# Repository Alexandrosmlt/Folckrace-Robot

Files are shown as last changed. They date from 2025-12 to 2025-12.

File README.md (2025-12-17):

# Folckrace Robot

## 1. Project Overview

#### This is an autonomous robot made for Folkrace (which is a robot competition centered around autonomous racing and steering skills). My design features 4 HS DC Motors paired with 5 ToF sensors, providing precise feedback in real time.

## 1.1 Why i am building this project

#### I am making this project to get real-life experience in developing complex systems and working with fast robotics controls. This project is great to help me improve my skills in putting together microcontrollers, motor drivers and sensors in order to create a autonomous and competitive robot.

## 2. Hardware and Design

### 2.1 3D Visualization

* **Front View**:

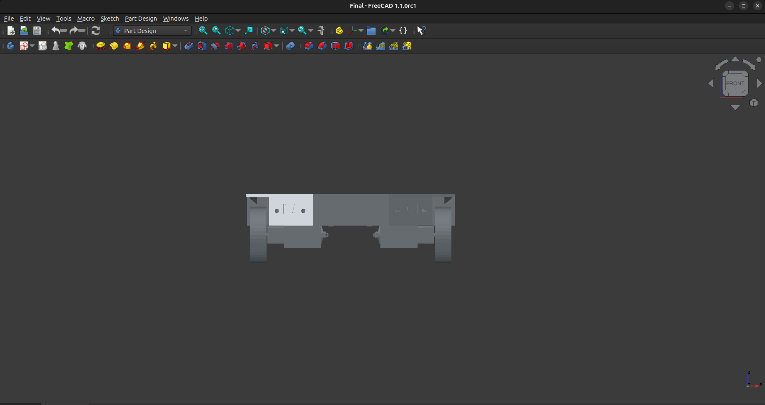
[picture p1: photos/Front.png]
Front

* **Rear View**:

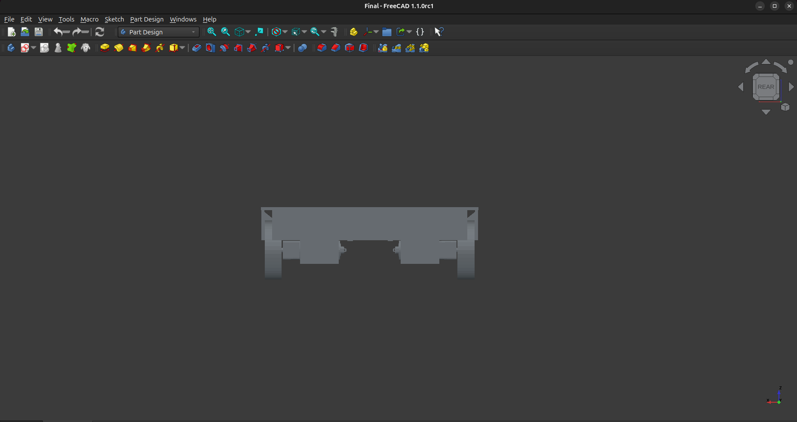
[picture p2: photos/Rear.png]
Rear

* **Right View**:

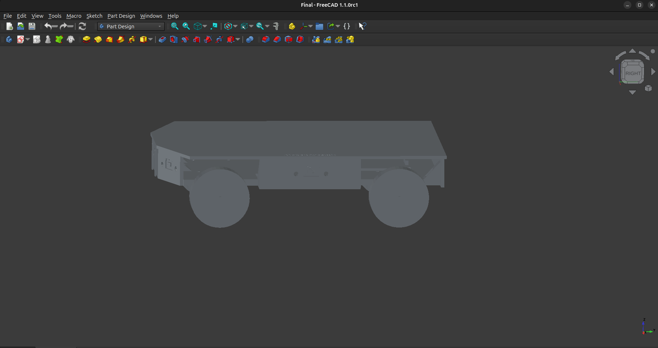
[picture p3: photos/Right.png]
Right

* **Left View**:

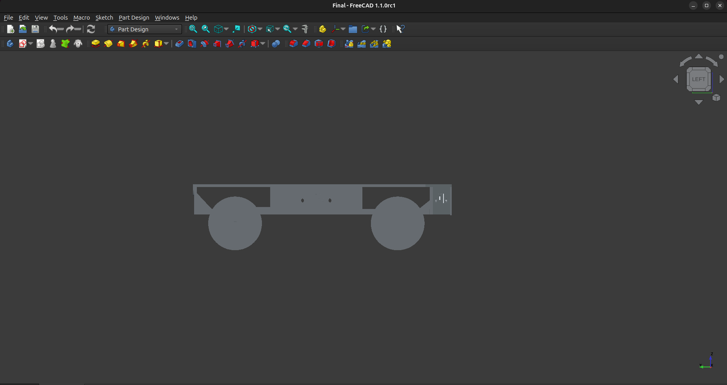
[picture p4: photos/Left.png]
Left

* **Final View**:

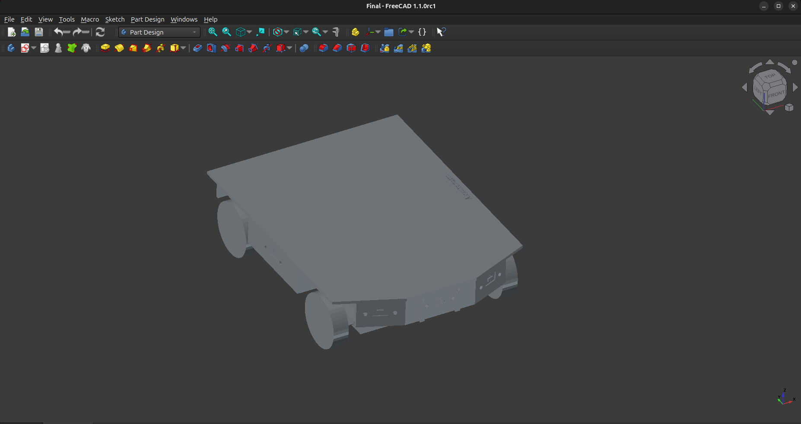
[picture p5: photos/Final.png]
Final


### 2.2 Custom PCB 

* **PCB Top View**:

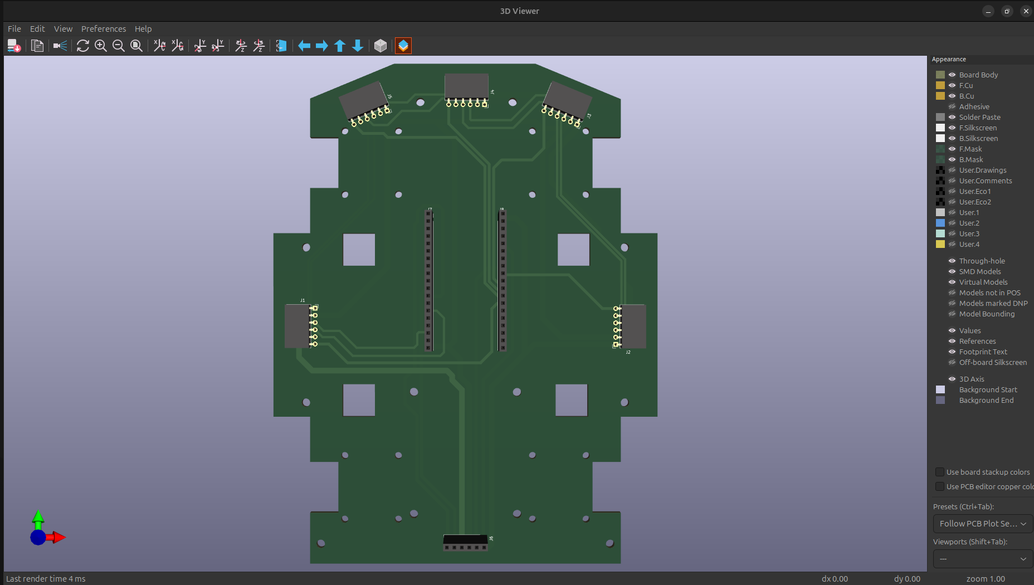
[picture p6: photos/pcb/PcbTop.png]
Top


* **PCB Bottom View**:

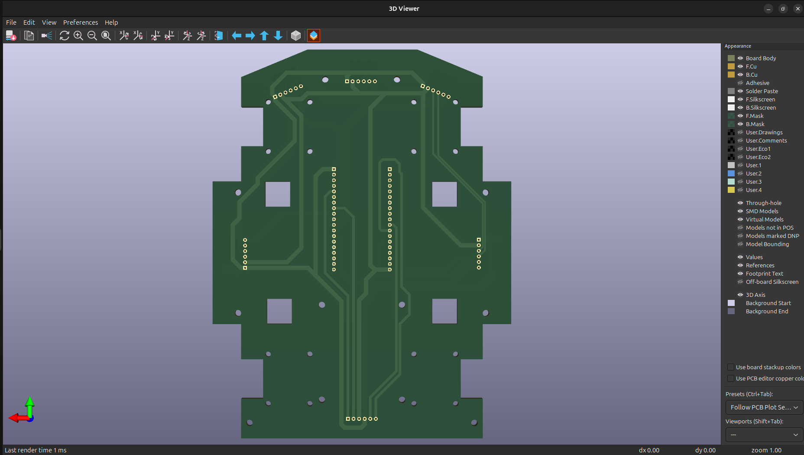
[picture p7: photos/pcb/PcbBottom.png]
Bottom


* **PCB Schematic**:

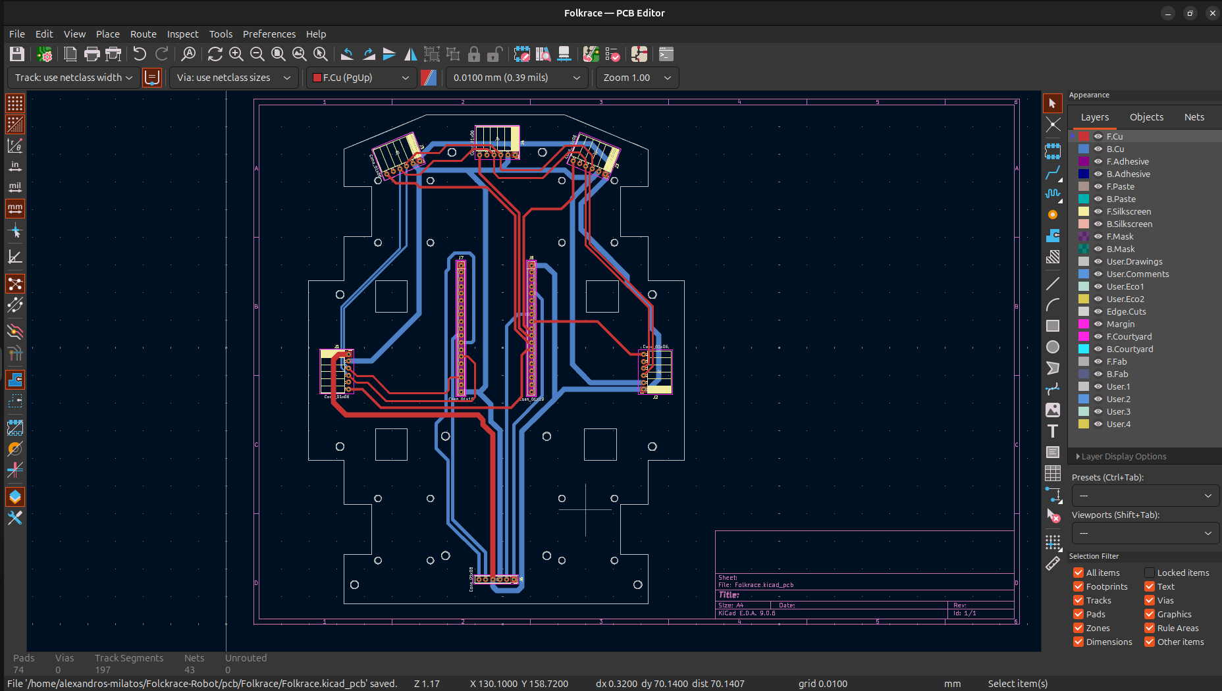
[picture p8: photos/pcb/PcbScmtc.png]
Schematic


### 2.3 Wiring Diagram

* **Wiring diagram**:

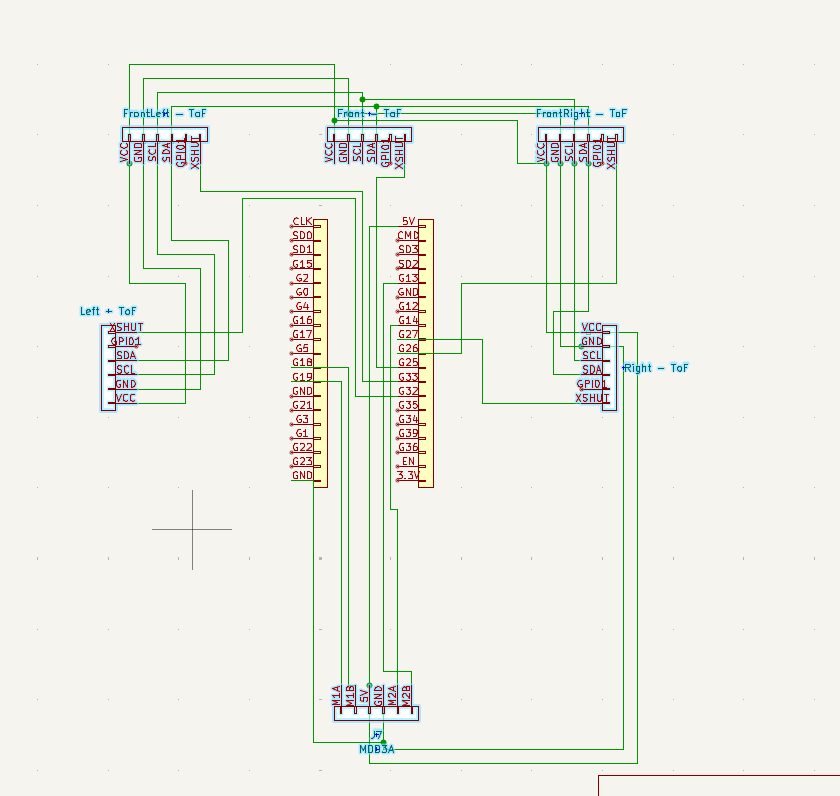
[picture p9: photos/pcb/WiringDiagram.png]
Wires!!


### 2.4 Pinout

#### 1. ToF Sensor Connections (5 Sensors)

>| Component | Function | ESP32 Pin |
>| :--- | :--- | :--- |
>| **I2C Bus** | Data Line (SDA) | **GPIO 21** |
>| **I2C Bus** | Clock Line (SCL) | **GPIO 22** |
>| ToF 1 | XSHUT Pin | **GPIO 33** |
>| ToF 2 | XSHUT Pin | **GPIO 32** |
>| ToF 3 | XSHUT Pin | **GPIO 27** |
>| ToF 4 | XSHUT Pin | **GPIO 26** |
>| ToF 5 | XSHUT Pin | **GPIO 25** |

#### Motor Driver (MDD3A)

>| MDD3A | Motor | Function | ESP32 Pin |
>| :--- | :--- | :--- | :--- |
>| M1A | Motor 1 | Forward Speed | **GPIO 19** |
>| M1B | Motor 1 | Reverse Speed | **GPIO 18** |
>| M2A | Motor 2 | Forward Speed | **GPIO 14** |
>| M2B | Motor 2 | Reverse Speed | **GPIO 13** |

#### 3. Total Used Pins

>| Type | Pin Numbers Used | Total |
>| :--- | :--- | :--- |
>| **Motor Driver (PWM)** | 19, 18, 14, 13 | 4 |
>| **I2C** | 21, 22 | 2 |
>| **ToF XSHUT** | 33, 32, 27, 26, 25 | 5 |
>| **TOTAL GPIO PINS USED** | | **11** |

## 3.Filmware

### Summury of [Code](/firmware/Folkrace.ino) (**NOT TESTED**):

#### 1.Setup: The ESP32 initializes Wi-Fi, OTA and I2C bus and configures all ToF's and assigns them a unique addresses.

#### 2.Imput: The main loop is reading the distance from all the sensors and compines them using weighted coefficients to calculate a single positional error.

#### 3.Control: It gets the error and feeds it in the PID controller, which calculates the correction needed to reduce the error to 0.

#### 4.Output: The correction finaly is applied to the motors using PWM signals.

## 3.1 Parts that require [3D printing](/STLs)

### Parts List:

* **[Front Bumper](/STLs/FrontBumper.stl)** (Quantity: 1)
* **[Rear Bumper](/STLs/RearBumper.stl)** (Quantity: 1)
* **[Side Bumpers](/STLs/SideBumper.stl)** (Quantity: 2)
* **[Motor Mounts](/STLs/MotorMount.stl)** (Quantity: 4)

<!-- ## 4. Bill of Materials (BOM)

| Item | Description | Quantity | Unit Price (€) | Total Price (€) | URL | Running Total (€ with Tax) |
| :--- | :--- | :--- | :--- | :--- | :--- | :--- |
| **DC Motors** | Drive Motors (6V 750RPM) | 4 | 16.00 | 64.00 | [https://www.jsumo.com](https://www.jsumo.com/core-dc-motor-6v-750rpm) | 64.00 |
| **Wheels** | Aluminum - Silicone Wheel Set | 2 | 15.50 | 31.00 | [https://www.jsumo.com](https://www.jsumo.com/jsumo-wheel-43x11mm-pair-soft-silicone) | 95.00 |
| **Microcontroller** | ESP32-DevKitC Development Board | 1 | 9.90 | 9.90 | [https://grobotronics.com](https://grobotronics.com/esp32-development-board-devkit-v1.html) | 104.90 |
| **Sensors** | VL53L0X Time-of-Flight (ToF) | 5 | 2.50 | 12.50 | [https://www.temu.com](https://www.temu.com/ul/kuiper/un9.html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) | 117.40 |
| **Motor Driver** | Cytron MDD3A | 1 | 8.50 | 8.50 | [https://botland.store](https://botland.store/motor-drivers-modules/15819-cytron-mdd3a-dual-channel-16v-3a-motor-controller-5904422324841.html) | 125.90 |
| **Battery** | Battery Lithium 18650 | 2 | 5.80 | 11.60 | [https://grobotronics.com](https://grobotronics.com/battery-lithium-18650-3.6v-3200mah-lg-inr18650-mh1.html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) | 137.50 |
| **Battery Holder** | Battery Holder 2×18650 with Plug 5.5×2.1 | 1 | 1 | 1 | [https://grobotronics.com](https://grobotronics.com/battery-holder-218650-with-plug-5-5x2-1.html) | 138.50 |
| **Pin Header** | Pin Header Female 1x6 2.54mm | 6 | 0.08 | 0.64 | [https://grobotronics.com](https://grobotronics.com/pin-header-1x6-female-2.54mm.html) | 139.14 |
| **Pin Header** | Pin Header 1x20 Female 2.54mm| 2 | 0.25 | 0.50 | [https://grobotronics.com](https://grobotronics.com/pin-header-1x20-female-2.54mm.html) | 139.64 |
| **PCB Manufacturing** | PCBWay | 5 | $47.78 | $75.75 | [https://www.pcbway.com](https://www.pcbway.com/QuickOrderOnline.aspx) | 215.39 |
 -->

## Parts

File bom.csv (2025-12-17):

Item | Description | Quantity | Notes
DC Motors | Drive motors (6V 750RPM) | 4 | Main drive motors
Wheels | Aluminum wheels with soft silicone | 2 | Compatible with DC motors
ESP32 Dev Board | ESP32-DevKitC development board | 1 | Main microcontroller, handles control logic
VL53L0X ToF Sensors | Time-of-Flight distance sensors | 5 | Used for obstacle detection / sensing
Cytron MDD3A Motor Driver | Dual channel 3A motor driver | 1 | Controls DC motors with PWM
18650 Lithium Batteries | 3.6V 18650 Li-ion cells | 2 | Main power source
Battery Holder | 2x18650 battery holder with DC plug | 1 | Holds and powers the system
Female Pin Headers 1x6 | 2.54mm female headers | 6 | For sensor and board connections
Female Pin Headers 1x20 | 2.54mm female headers | 2 | For ESP32 and PCB connections
Custom PCB | Manufactured PCB (PCBWay) | 5 | Main circuit boards

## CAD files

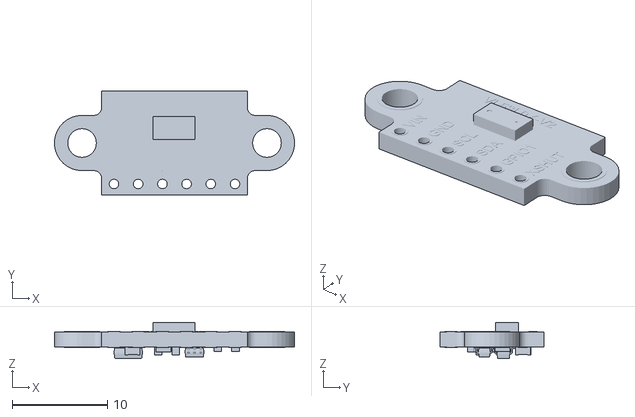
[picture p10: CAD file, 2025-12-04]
cad/3D parts/VL53L0X-V2.stl
25.2 x 10.9 x 3.80

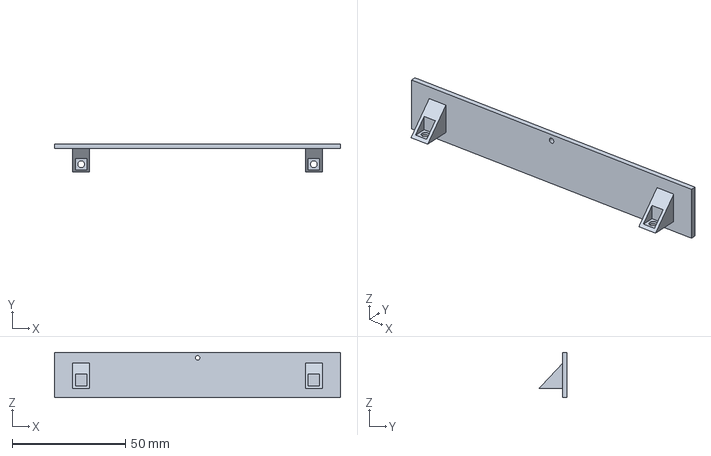
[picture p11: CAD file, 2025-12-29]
cad/RearBumper.FCStd
126.0 x 12.5 x 20.0 mm

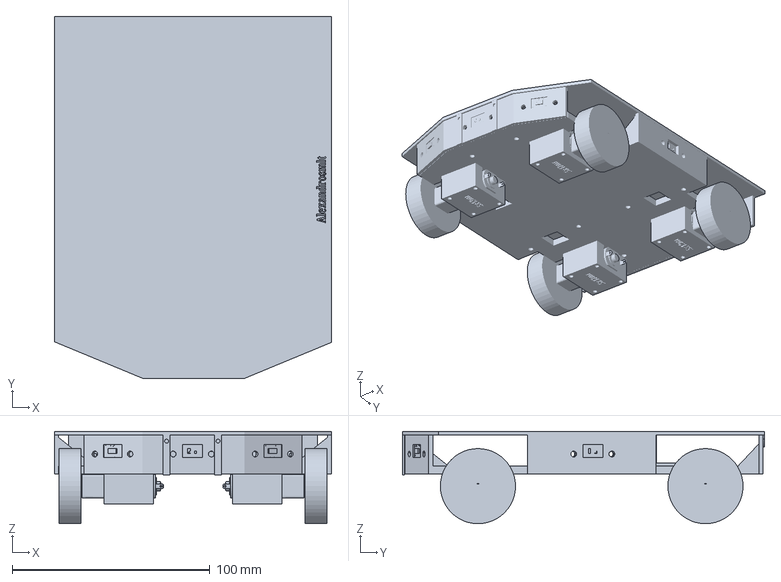
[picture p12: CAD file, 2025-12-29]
cad/Final.FCStd
140.1 x 183.1 x 46.7 mm

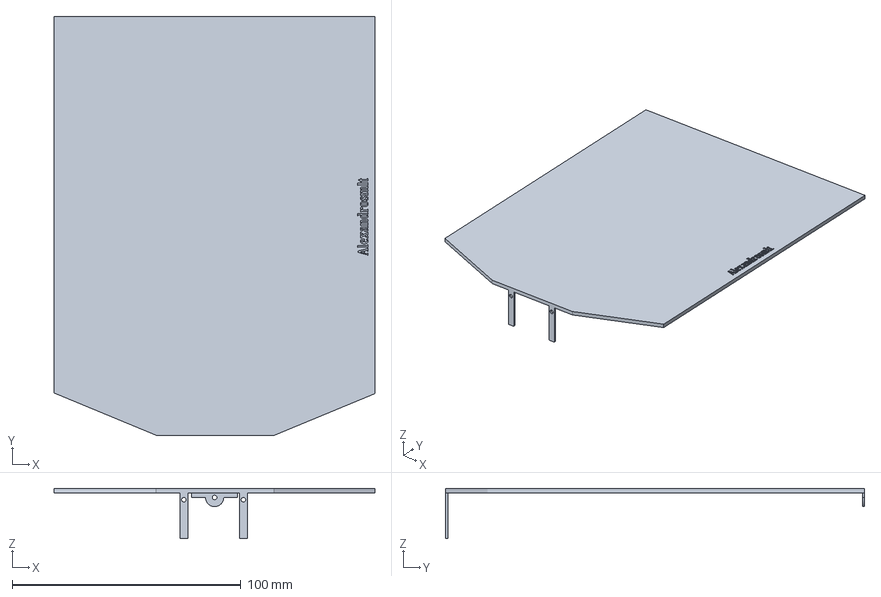
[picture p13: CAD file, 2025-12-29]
cad/TopCover.FCStd
140.1 x 183.0 x 22.0 mm

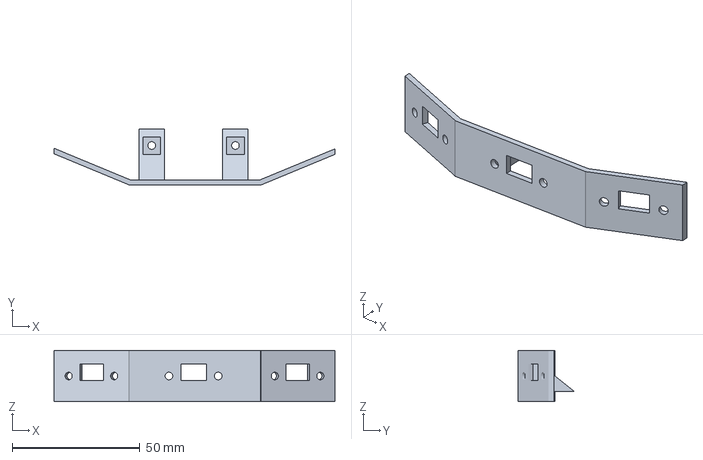
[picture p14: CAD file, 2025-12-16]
cad/FrontBumper.FCStd
110.0 x 22.0 x 20.0 mm

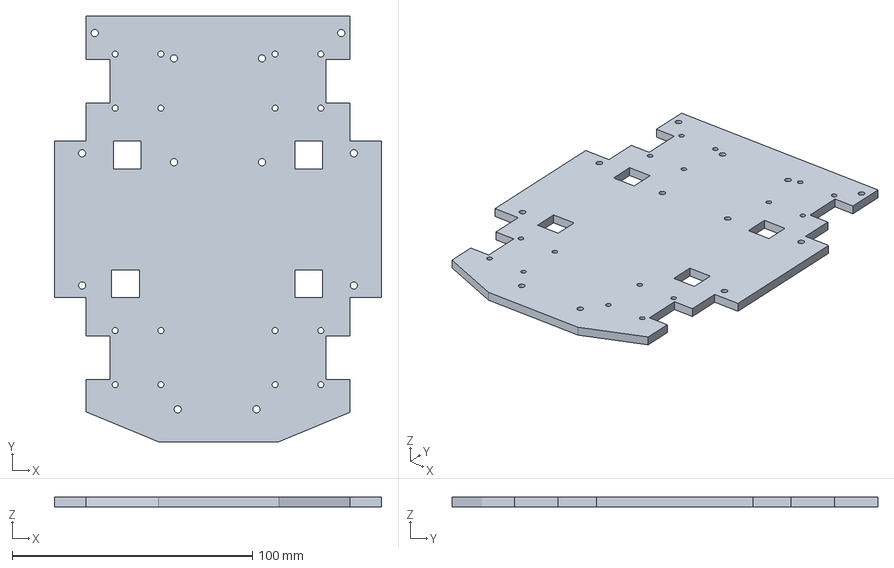
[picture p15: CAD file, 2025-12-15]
cad/Base.FCStd
136.0 x 177.0 x 4.00 mm

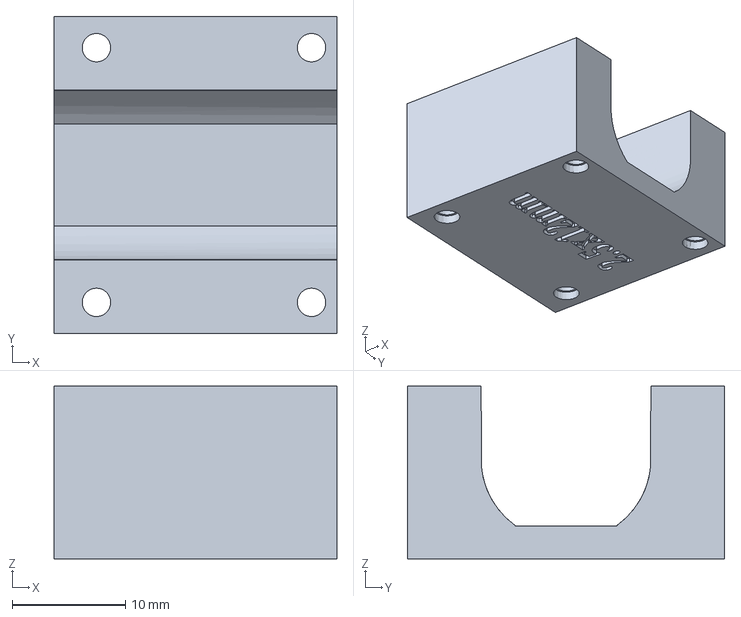
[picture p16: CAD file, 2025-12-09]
cad/MotorMount.FCStd
25.0 x 28.0 x 15.2 mm

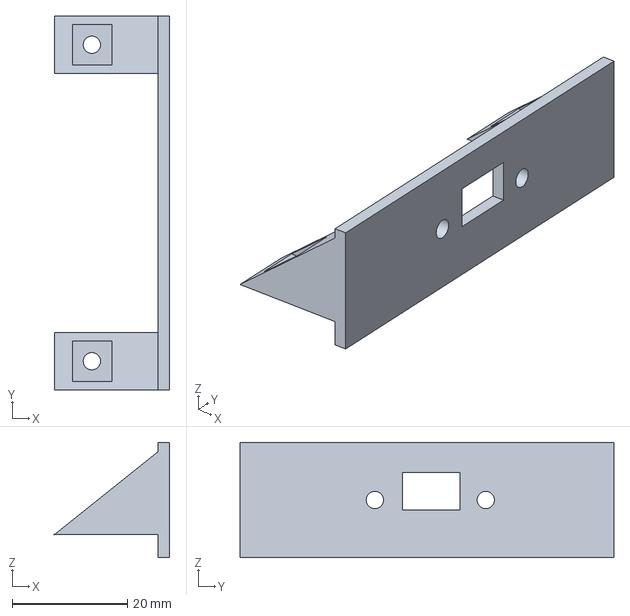
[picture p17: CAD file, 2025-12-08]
cad/SideBumper.FCStd
20.0 x 65.0 x 20.0 mm

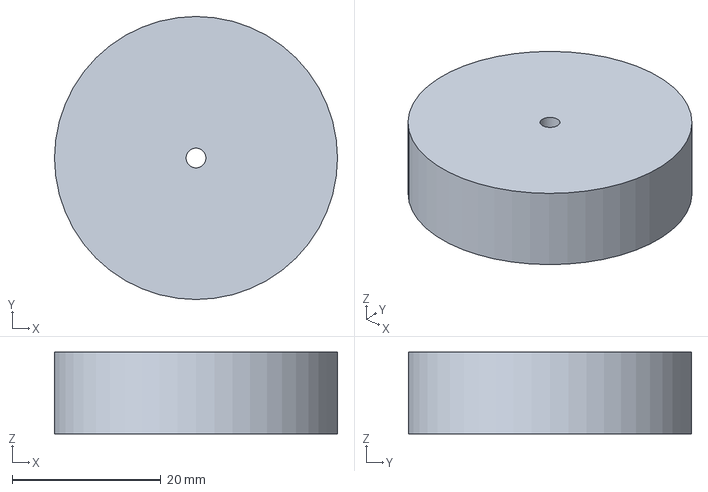
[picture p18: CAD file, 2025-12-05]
cad/Wheel.FCStd
38.0 x 38.0 x 11.0 mm

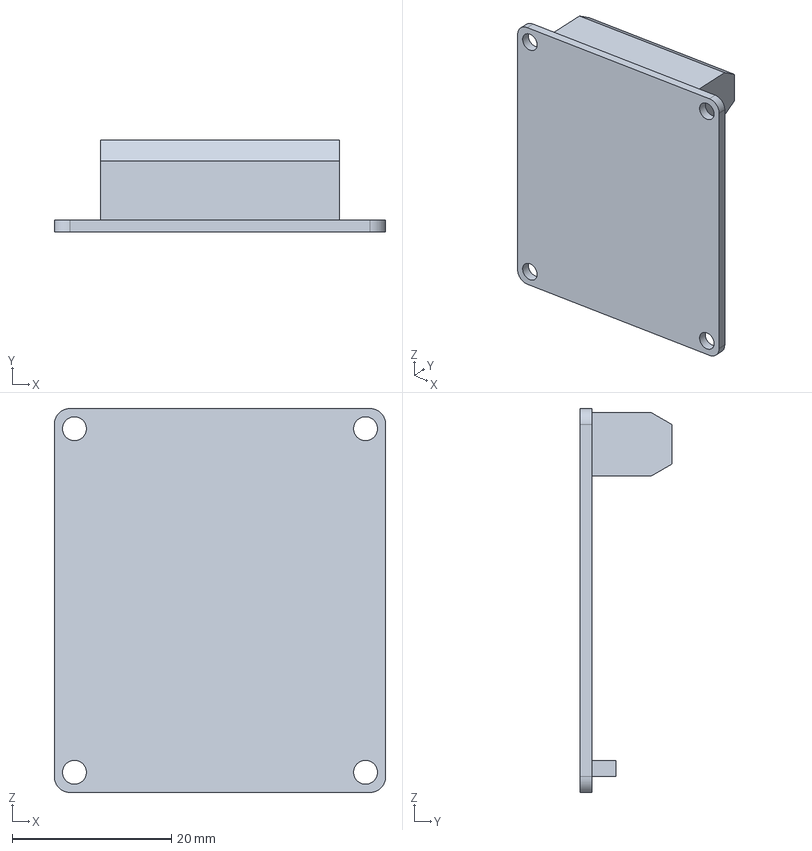
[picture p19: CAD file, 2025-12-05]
cad/CYTRON-MDD3A.FCStd
41.7 x 11.5 x 48.3 mm

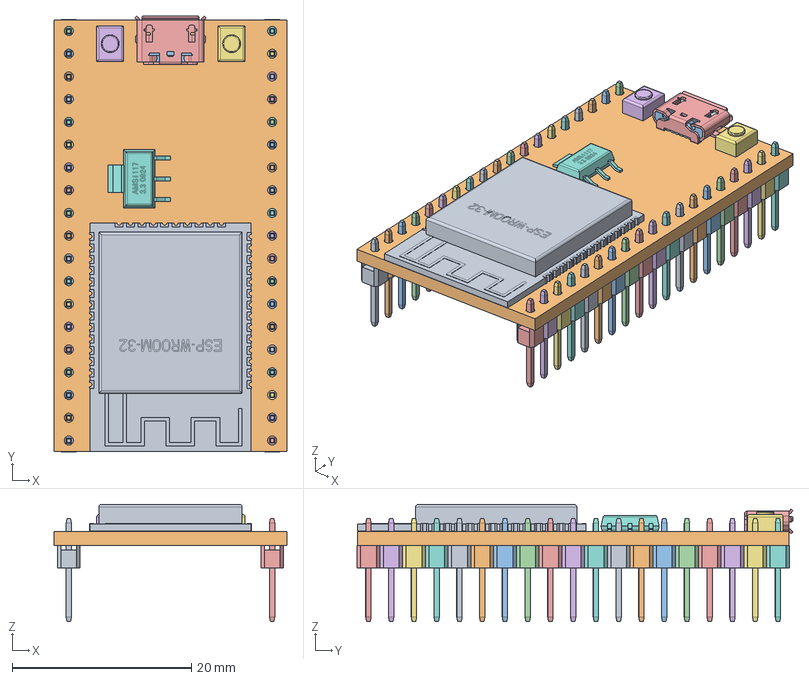
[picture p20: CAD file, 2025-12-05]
cad/ESP32.FCStd
26.0 x 48.7 x 13.1 mm
KiCAD-ESP-WROOM-32
ESP32 PCB
molex_0473460001
molex_0473460002
molex_0473460003
button
button001
AMS1117
HEADER10P
HEADER10P001
HEADER10P002
HEADER10P003
HEADER10P004
HEADER10P005
HEADER10P006
HEADER10P007
HEADER10P008
HEADER10P009
HEADER10P011
HEADER10P012
HEADER10P013
HEADER10P014
HEADER10P015
HEADER10P016
HEADER10P017
HEADER10P018
HEADER10P019
HEADER10P020
HEADER10P022
HEADER10P023
HEADER10P024
HEADER10P025
HEADER10P026
HEADER10P027
HEADER10P028
HEADER10P029
HEADER10P030
HEADER10P031
HEADER10P033
HEADER10P034
HEADER10P035
HEADER10P036
HEADER10P037
HEADER10P038
HEADER10P039
HEADER10P040
HEADER10P041
HEADER10P042

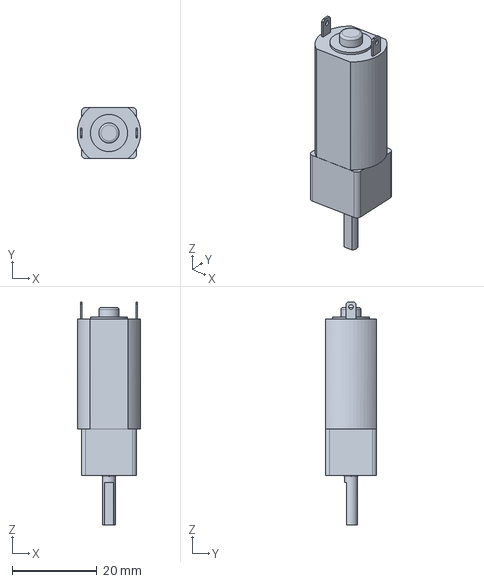
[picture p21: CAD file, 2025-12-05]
cad/DcMotor.FCStd
15.0 x 12.1 x 52.7 mm

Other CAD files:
cad/BaseTraces.FCStd
cad/VL53L0X.FCStd
STLs/FrontBumper.stl
STLs/MotorMount.stl
STLs/RearBumper.stl
STLs/SideBumper.stl
cad/3D parts/Base.stl
cad/3D parts/CYTRON-MDD3A.stl
cad/3D parts/DcMotor.stl
cad/3D parts/ESP32.stl
cad/3D parts/Final.stl
cad/3D parts/MotorMount.stl
cad/3D parts/RearBumper.stl
cad/3D parts/TopCover.stl
cad/3D parts/Wheel.stl

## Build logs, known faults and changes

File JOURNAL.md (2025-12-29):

## FOLCKRACE ROBOT

## Total Time Spent: ~ 15h

# UPDATES

**Date:** 2025-12-29

### Task: Hardware Modeling
* **Component:** Rear Bumper Bumpers
* **Work Performed:** Made a 2mm hole for the screw from `TopCover.stl`
* **File Output:** `RearBumper.stl`
* **Status:** Complete
* **Time Spent:** ~0.40h
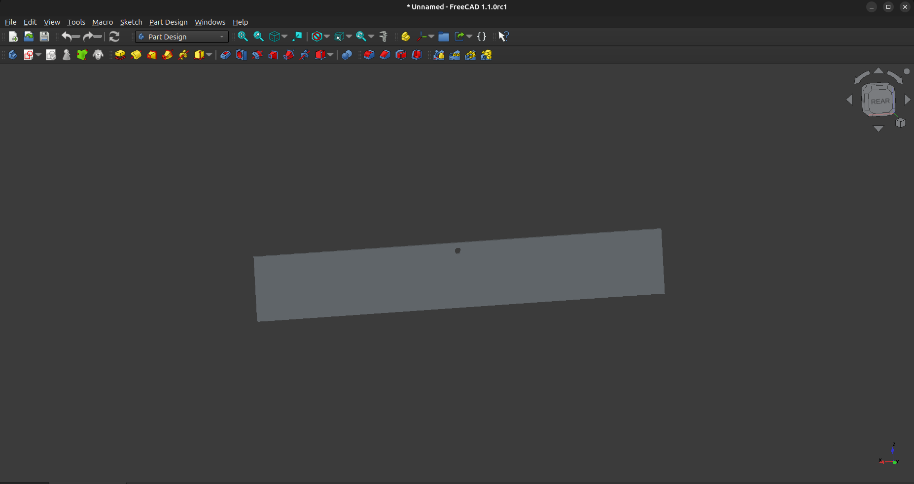
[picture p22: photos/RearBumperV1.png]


### Task: Hardware Modeling
* **Component:** Top Cover
* **Goal:** Make something to cover the top of the robot 
* **Work Performed:** Made the top cover for the robot
* **File Output:** `TopCover.stl`
* **Status:** Complete.
* **Time Spent:** ~0.40h
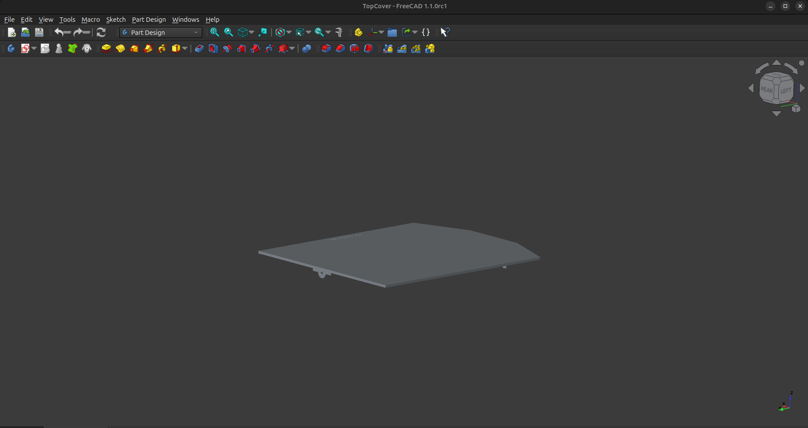
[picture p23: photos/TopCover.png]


**Date:** 2025-12-16

### Task: Filmware
* **Goal:** Make The code for the ESP32
* **Work Performed:** Made a completed version for the Robot that uses OTA for updates and PID to calculate the weight which gets processed and drives the motors to zero error.
* **Status:** Complete.
* **Time Spent:** ~1.30h
* [Code](/firmware/Folkrace.ino)

# PCB MODELING COMPLETED

## **Final PCB:**

Final

# CUSTOM PCB

### Task: PCB Modeling
* **Component:** PCB
* **Goal:** Finish the PCB.
* **Work Performed:** Placed the connectors and connected everything in a 2 layer PCB
* **Status:** Complete.
* **Time Spent:** ~2.30h
Status

**Date:** 2025-12-15

### Task: PCB Modeling
* **Component:** PCB
* **Goal:** Make the edge cuts for the PCB.
* **Work Performed:** Made the edge cuts and added the compoments to the pcb editor
* **Status:** Complete.
* **Time Spent:** ~0.30h
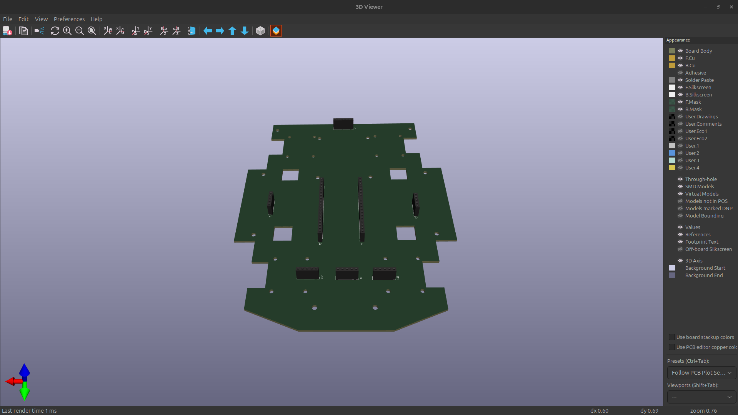
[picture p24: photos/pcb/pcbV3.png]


### Task: Hardware Modeling
* **Component:** Base
* **Goal:** Make .svg for the PCB
* **Work Performed:** Made the base with graphics to put everything together
* **Status:** Complete.
* **Time Spent:** ~0.40h
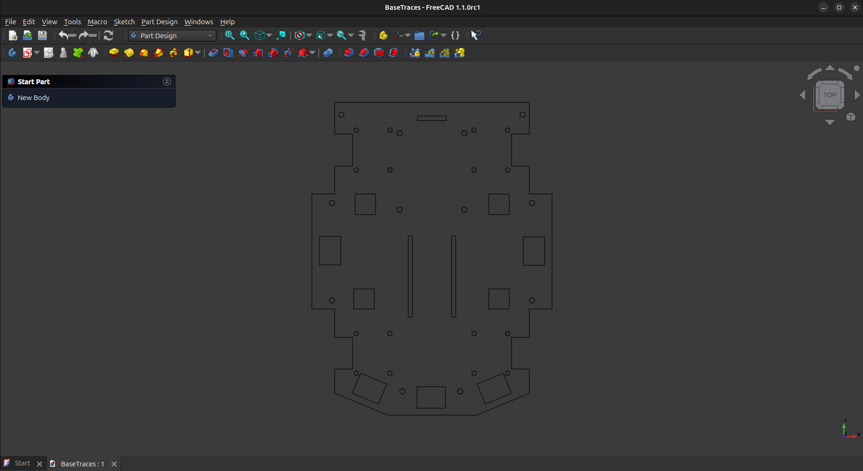
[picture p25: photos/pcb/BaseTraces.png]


**Date:** 2025-12-13

### Task: PCB Modeling
* **Component:** PCB
* **Goal:** Continue making the symbols to start the PCB.
* **Work Performed:** Custom symbols for the ESP32 and MDD3A were created in **KiCAD** and the compoments were all connected together.
* **Status:** Complete.
* **Time Spent:** ~0.50h
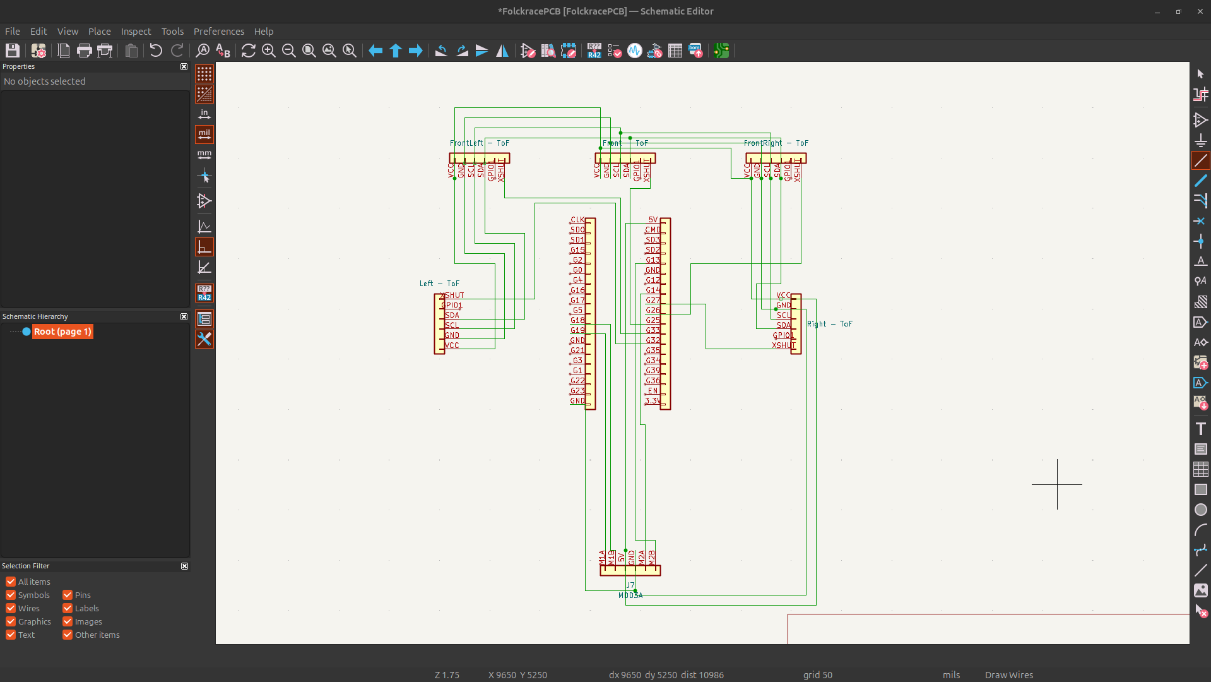
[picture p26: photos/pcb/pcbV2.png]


**Date:** 2025-12-11

### Task: PCB Modeling
* **Component:** PCB
* **Goal:** Make the symbols to start the PCB.
* **Work Performed:** Made a custom symbol for the ToF sensors in **KiCAD**. Next i will create the symbols for the esp32 and mdd3a motor driver
* **Status:** Complete.
* **Time Spent:** ~0.10h
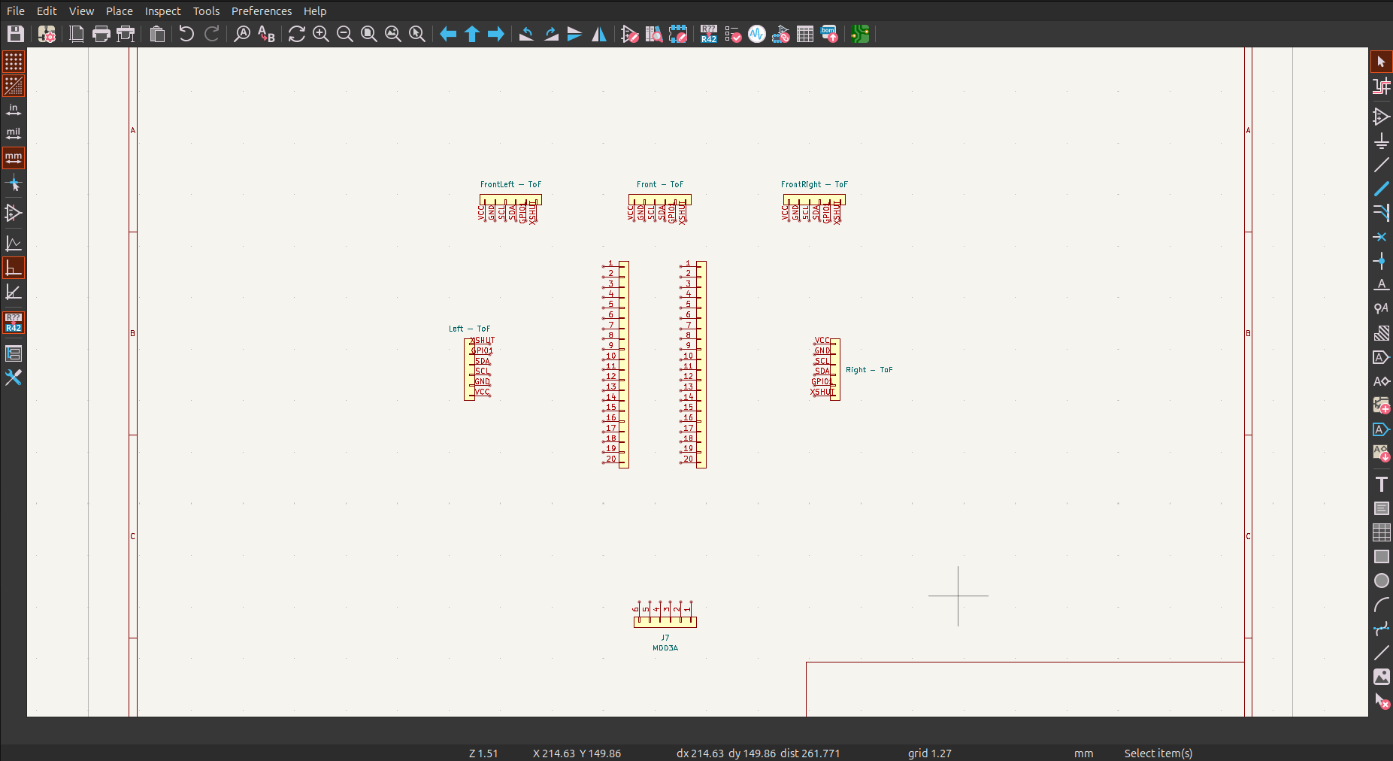
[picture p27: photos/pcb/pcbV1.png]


**Date:** 2025-12-09

# HARDWARE MODELING COMPLETED

## **Final 3D Visualization:**

Final

### Task: Hardware Modeling
* **Component:** Base
* **Goal:** Create a 3D model for the robots base.
* **Work Performed:** Updated the base in **FreeCAD** to include 3mm holes for the `RearBumper.stl`
* **File Output:** `Base.stl`
* **Status:** Complete, Ready for use.
* **Time Spent:** ~0.10h
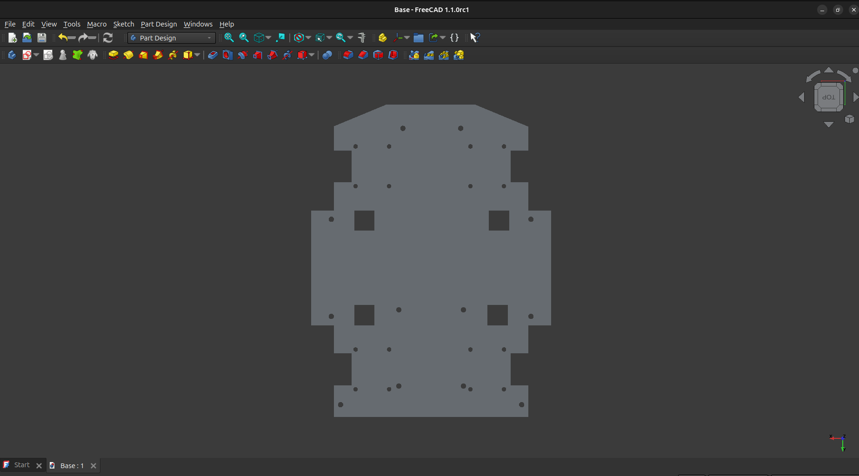
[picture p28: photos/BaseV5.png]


### Task: Hardware Modeling
* **Component:** Side Bumpers
* **Goal:** Create a 3D model for the 2 side sensors to mount on.
* **Work Performed:** Designed a back bumper model in **FreeCAD** to protect the robot 
* **File Output:** `RearBumper.stl`
* **Status:** Complete, Ready for testing 
* **Time Spent:** ~0.40h
Status

### Task: Hardware Modeling
* **Component:** Base
* **Goal:** Create a 3D model for the robots base.
* **Work Performed:** Updated the base in **FreeCAD** to include 11.5mm holes for the motor cables
* **File Output:** `Base.stl`
* **Status:** Complete, Ready for use.
* **Time Spent:** ~0.10h
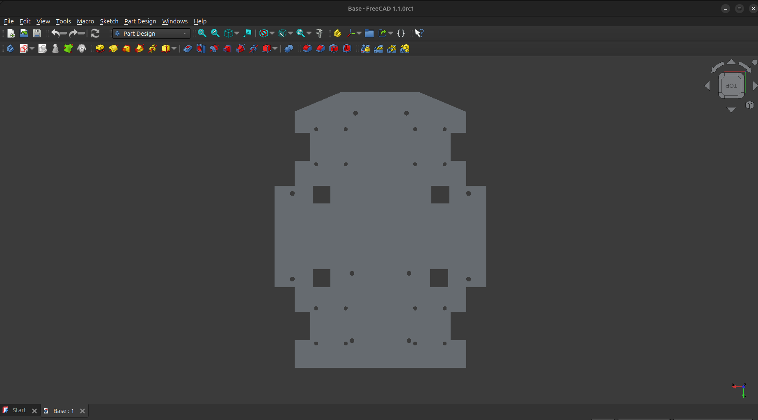
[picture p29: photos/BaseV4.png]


**Date:** 2025-12-08

### Task: Hardware Modeling
* **Component:** Base
* **Goal:** Create a 3D model for the robots base.
* **Work Performed:** Updated the base in **FreeCAD** to include 3mm holes for the motor driver (`CYTRON-MDD3A.stl`)
* **File Output:** `Base.stl`
* **Status:** Complete, Ready for use.
* **Time Spent:** ~0.10h
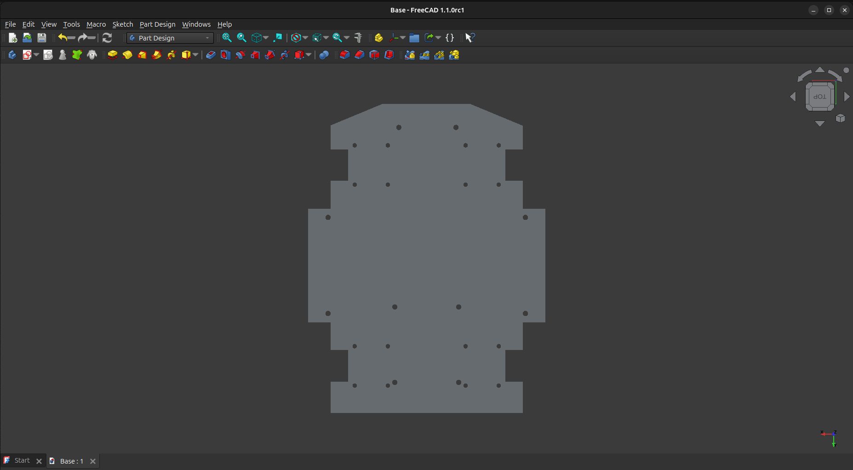
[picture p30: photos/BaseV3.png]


### Task: Hardware Modeling
* **Component:** Base
* **Goal:** Create a 3D model for the robots base.
* **Work Performed:** Updated the base in **FreeCAD** to include 3mm holes for `SideBumper.stl` and `FrontBumper.stl`
* **File Output:** `Base.stl`
* **Status:** Complete, Ready for use.
* **Time Spent:** ~0.30h
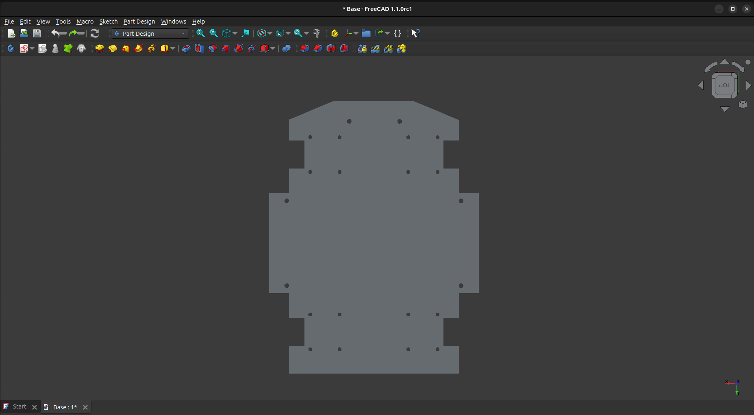
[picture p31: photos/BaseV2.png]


### Task: Hardware Modeling
* **Component:** Side Bumpers
* **Goal:** Create a 3D model for the 2 side sensors to mount on.
* **Work Performed:** Designed a single side bumper model in **FreeCAD** for the ToF sensors to mount on, which is the same for each side of the robot
* **File Output:** `SideBumper.stl`
* **Status:** Complete, Ready for printing 
* **Time Spent:** ~1.00h
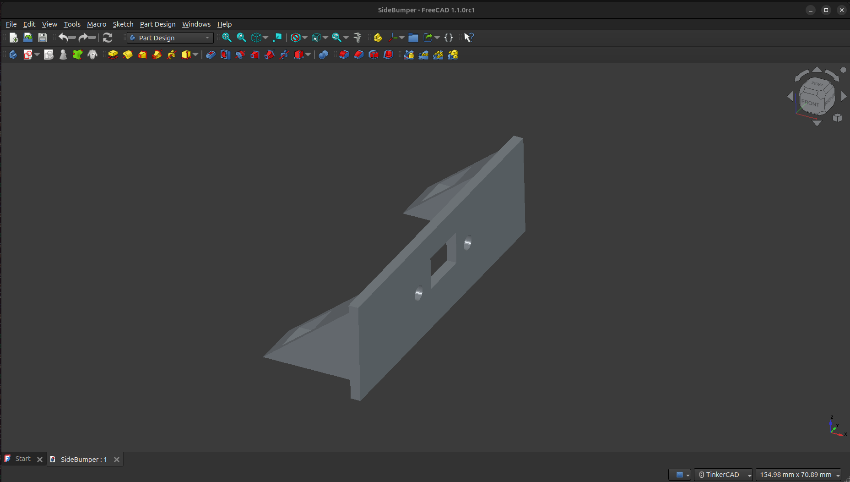
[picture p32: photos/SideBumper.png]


**Date:** 2025-12-06

### Task: Hardware Modeling
* **Component:** Front Bumper
* **Goal:** Create a 3D model for the front sensors to mount on.
* **Work Performed:** Designed a front bumper in **FreeCAD** for the ToF sensors to mount on
* **File Output:** `FrontBumper.stl`
* **Status:** Complete, Ready for printing 
* **Time Spent:** ~1.20h
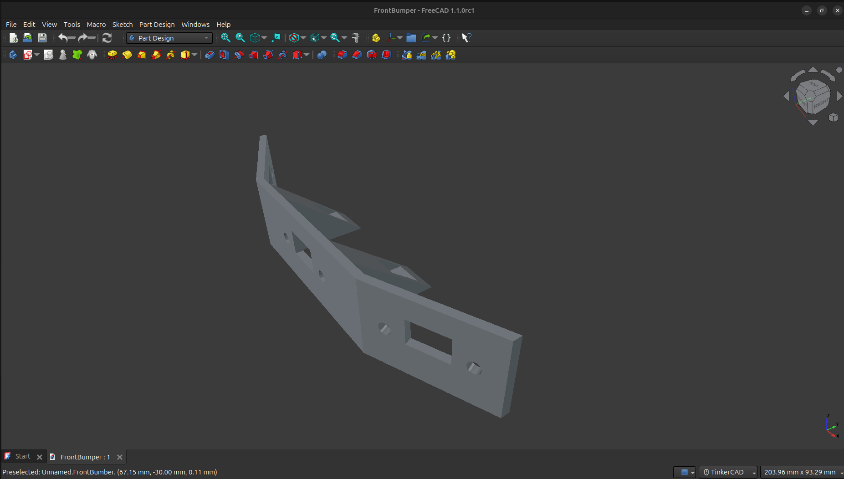
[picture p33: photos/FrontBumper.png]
* **File Output:** `Wheel.stl`

### Task: Hardware Modeling
* **Component:** Base
* **Goal:** Create a 3D model for the robots base.
* **Work Performed:** Designed a base in **FreeCAD** , made holes for `MotorMount.stl` and added space for the wheels
* **File Output:** `Base.stl`
* **Status:** Complete, Ready for use.
* **Time Spent:** ~0.30h
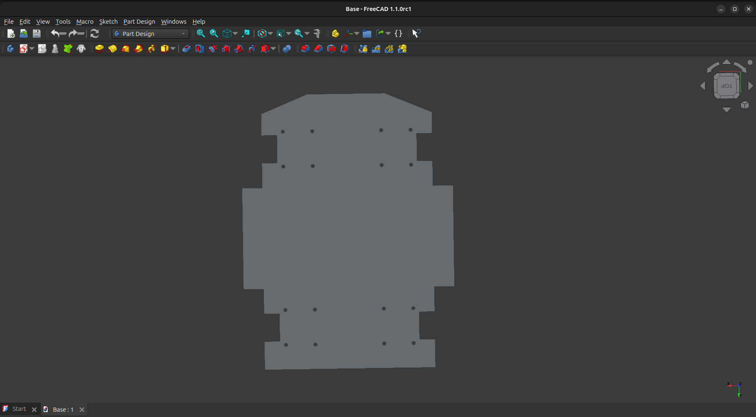
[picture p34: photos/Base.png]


**Date:** 2025-12-05

### Task: Hardware Modeling
* **Component:** Wheels
* **Goal:** Create a 3D model for the wheels
* **Work Performed:** The wheel was modeled in **FreeCAD** 
* **File Output:** `Wheel.stl`
* **Status:** Complete, Ready for import.
* **Time Spent:** ~0.15h
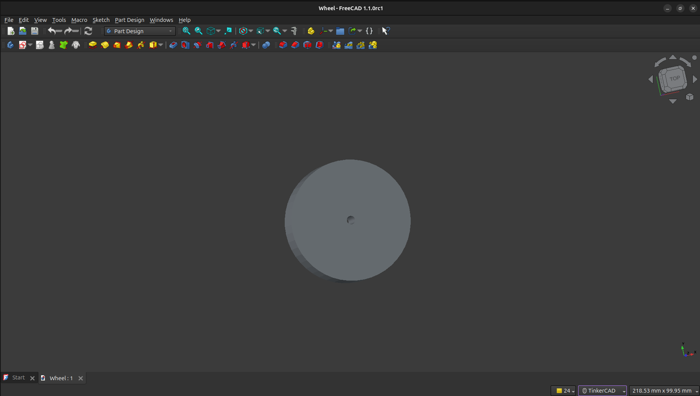
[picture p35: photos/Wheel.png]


### Task: Hardware Modeling
* **Component:** Motor Mount
* **Goal:** Design and create a 3D model for mounting x4 DC Motors to the chassis later on.
* **Work Performed:** After printing and testing `MotorMount.stl`, the screws weren't fitting properly. 
  The screw hole was enlarged for the head of the screw to fit and dimensions for the srcews are now written on the back of the mount.
* **File Output:** `MotorMount.stl`
* **Status:** Complete, Ready for printing and testing.
* **Time Spent:** ~0.30h
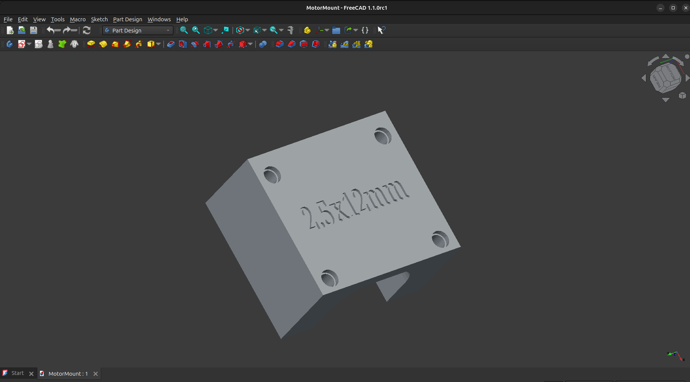
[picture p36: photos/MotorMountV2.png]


### Task: Hardware Modeling
* **Component:** Motor Mount 
* **Goal:** Design and create a 3D model for mounting x4 DC Motors to the chassis later on.
* **Work Performed:** The motor mount was modeled in **FreeCAD** 
* **File Output:** `MotorMount.stl`
* **Status:** Complete, Ready for printing and testing.
* **Time Spent:** ~0.50h
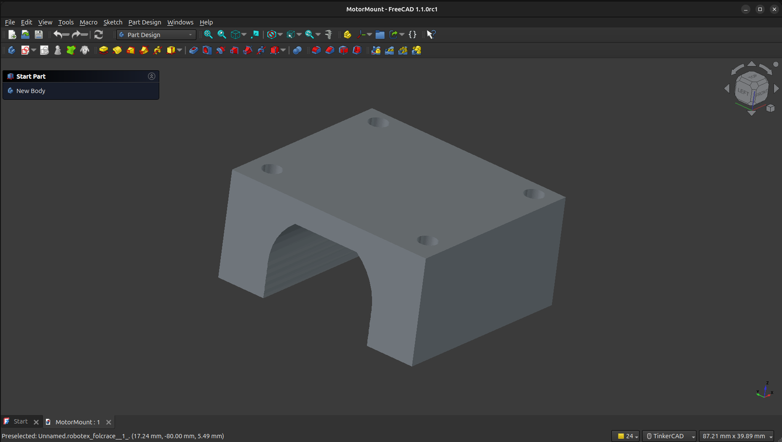
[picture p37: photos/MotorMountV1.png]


### Task: Hardware Modeling
* **Component:** ESP-32-DEV board
* **Goal:** Create an accurate 3D model of the ESP32 board.
* **Work Performed:** -None- The model was found in **[GrabCAD](https://grabcad.com/library/esp-32-dev-board-1)** 
* **File Output:** `ESP32.stl`
* **Status:** Complete, Ready for import.
* **Time Spent:** ~0.10h
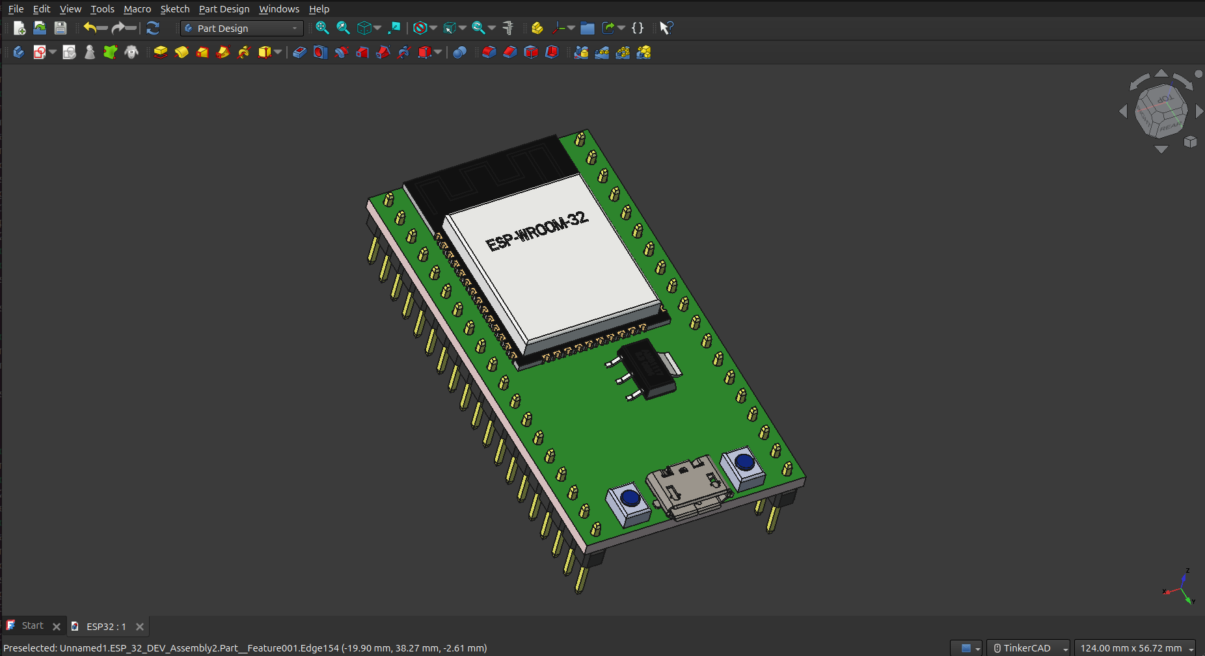
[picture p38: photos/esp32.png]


### Task: Hardware Modeling
* **Component:** Drive Motors (6V 750RPM)
* **Goal:** Create an accurate 3D model of the Motors.
* **Work Performed:** -None- The model was found in **[JSumo](https://www.dropbox.com/scl/fi/laliptgsevf1lr142pr5u/core-dc-motor-cad.rar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)** 
* **File Output:** `DcMotor.stl`
* **Status:** Complete, Ready for import.
* **Time Spent:** ~0.10h
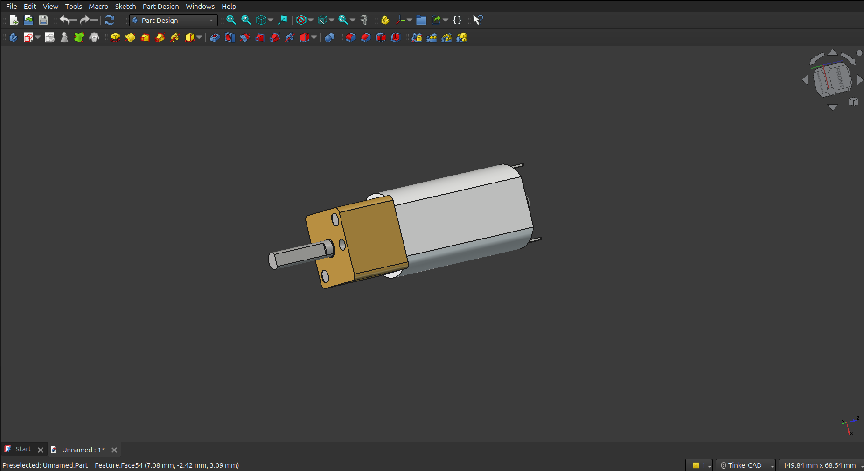
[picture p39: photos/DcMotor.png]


### Task: Hardware Modeling
* **Component:** Drive Motors (6V 750RPM)
* **Goal:** Create an accurate 3D model of the Motors.
* **Work Performed:** The board was modeled in **FreeCAD** 
* **File Output:** `CYTRON-MMD3A.stl`
* **Status:** Complete, Ready for import.
* **Time Spent:** ~0.30h
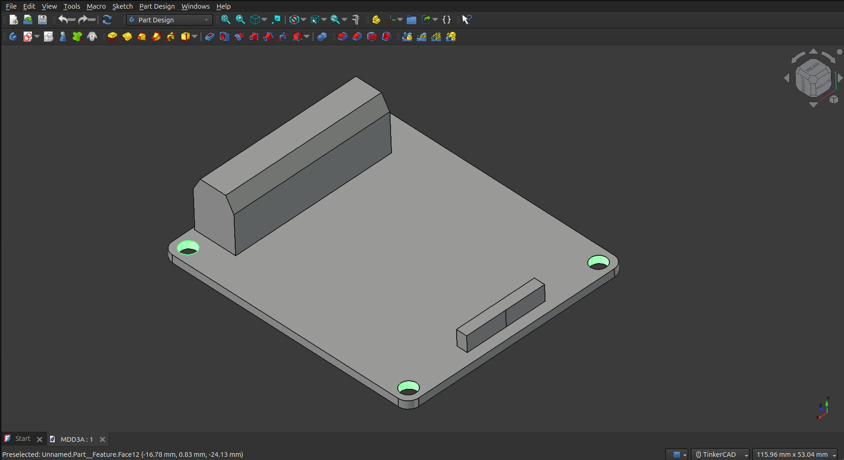
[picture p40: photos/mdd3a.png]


**Date:** 2025-12-04

### Task: Hardware Modeling
* **Component:** VL53L0X-V2 (ToF) Sensor
* **Goal:** Create an accurate 3D model of the ToF sensor.
* **Work Performed:** The sensor was modeled in **FreeCAD** 
* **File Output:** `VL53L0X-V2.stl`
* **Status:** Complete, Ready for import.
* **Time Spent:** ~1.30h
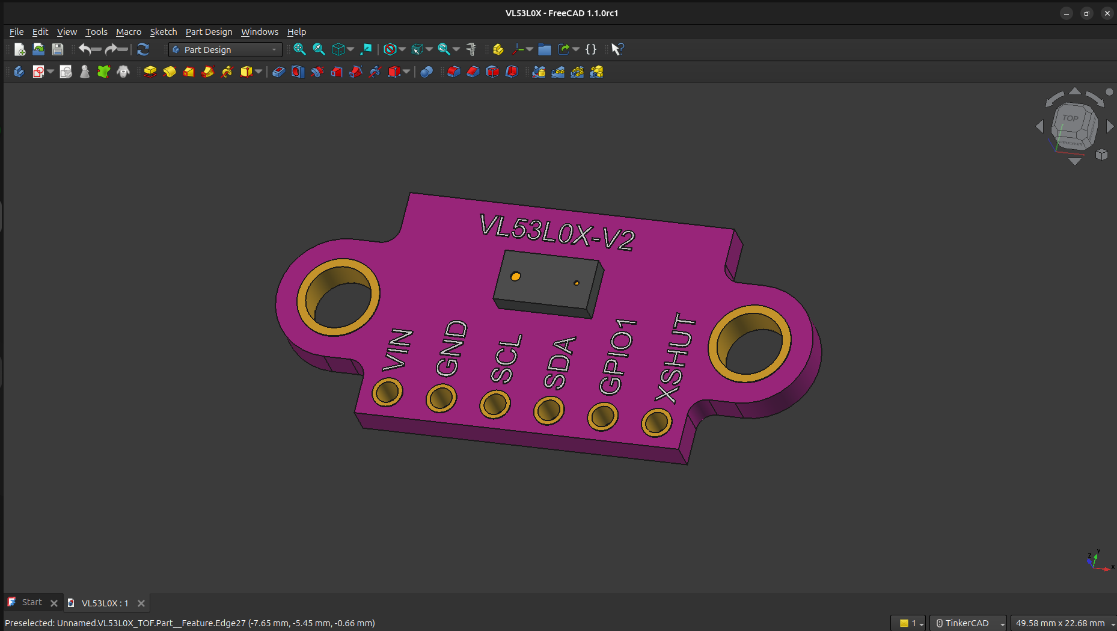
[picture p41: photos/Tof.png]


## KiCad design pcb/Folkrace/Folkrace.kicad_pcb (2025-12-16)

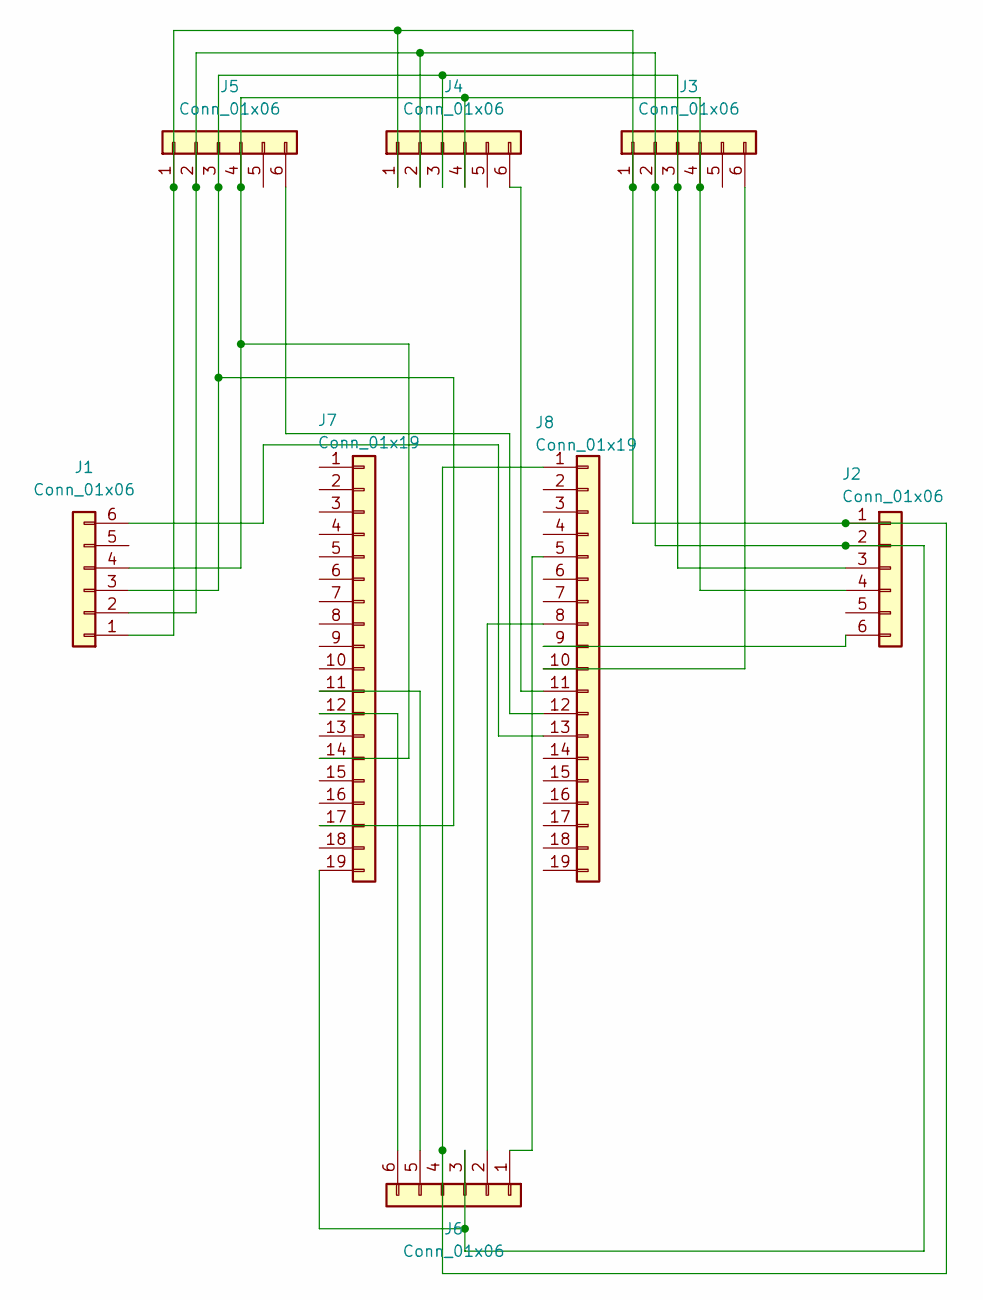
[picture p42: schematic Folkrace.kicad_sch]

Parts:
J1, J2, J3, J4, J5: Conn_01x06; PinSocket_1x06_P2.54mm_Horizontal
J6: Conn_01x06; PinSocket_1x06_P2.54mm_Vertical
J7, J8: Conn_01x19; PinSocket_1x19_P2.54mm_Vertical

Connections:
unnamed: J1.1, J2.1, J3.1, J4.1, J5.1, J6.4, J8.1
unnamed: J1.2, J2.2, J3.2, J4.2, J5.2, J6.3, J7.19
unnamed: J1.3, J2.3, J3.3, J4.3, J5.3, J7.17
unnamed: J1.4, J2.4, J3.4, J4.4, J5.4, J7.14
unnamed: J1.6, J8.13
unnamed: J2.6, J8.9
unnamed: J3.6, J8.10
unnamed: J4.6, J8.11
unnamed: J5.6, J8.12
unnamed: J6.1, J8.5
unnamed: J6.2, J8.8
unnamed: J6.5, J7.11
unnamed: J6.6, J7.12

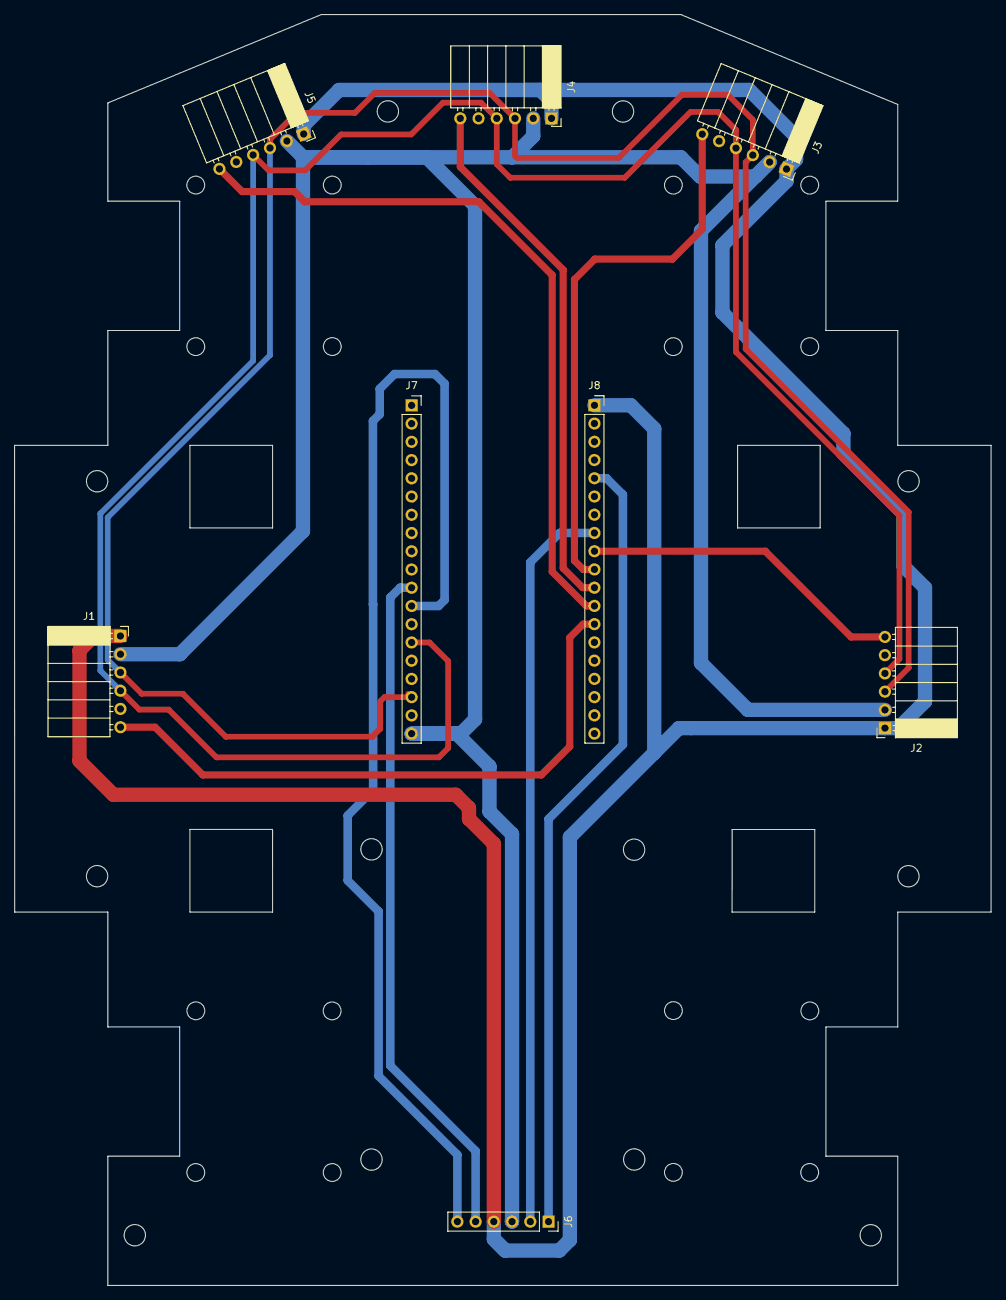
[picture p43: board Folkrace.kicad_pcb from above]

Board: 2 copper layers, 136.0 x 177.0 mm, 8 parts (0 on the bottom side), 13 nets.

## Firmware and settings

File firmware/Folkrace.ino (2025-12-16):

#include <WiFi.h>
#include <ArduinoOTA.h>
#include <Wire.h>
#include <Adafruit_VL53L0X.h>

#define I2C_SDA_PIN 21
#define I2C_SCL_PIN 22

const uint8_t XSHUT_PINS[] = {33, 32, 27, 26, 25};
#define NUM_SENSORS (sizeof(XSHUT_PINS) / sizeof(XSHUT_PINS[0]))

const int MD[2] = {19, 18}; 
const int SensorIndex[5] = {0, 1, 2, 3, 4}; 

int weights[5] = {-2, -1, 0, 1, 2}; 

Adafruit_VL53L0X lox_sensors[NUM_SENSORS];
const uint8_t NEW_I2C_ADDRESSES[] = {0x30, 0x31, 0x32, 0x33, 0x34}; 

const char* ssid = "Billys";
const char* password = "12345678";

unsigned long lastTime = 0;
float dt = 0.0001;

float Kp = 150;
float Ki = 0;
float Kd = 0;

float error = 0;
float integral = 0;
float previous_error = 0;

const int baseSpeed = 200;

const int bootButtonPin = 0;
bool motorsEnabled = false;
bool lastButtonState = HIGH;
unsigned long lastDebounceTime = 0;
const unsigned long debounceDelay = 50;

void tof_init() {
  for (int i = 0; i < NUM_SENSORS; i++) {
    pinMode(XSHUT_PINS[i], OUTPUT);
    digitalWrite(XSHUT_PINS[i], LOW);
  }
  delay(10); 

  for (int i = 0; i < NUM_SENSORS; i++) {
    digitalWrite(XSHUT_PINS[i], HIGH); 
    delay(10); 
    
    lox_sensors[i] = Adafruit_VL53L0X();
    if (!lox_sensors[i].begin()) {
      
    } else {
        lox_sensors[i].setAddress(NEW_I2C_ADDRESSES[i]);
    }
  }
}

int read_tof_distance(int sensor_index) {
  VL53L0X_RangingMeasurementData_t measure;
  lox_sensors[sensor_index].rangingTest(&measure, false); 
  
  if (measure.RangeStatus != 4) {
      int distance = measure.RangeMilliMeter;
      int mapped_value = map(distance, 500, 50, 0, 1000); 
      
      return constrain(mapped_value, 0, 1000);
  } else {
      return 0; 
  }
}

void setup() {
    WiFi.mode(WIFI_AP);
    WiFi.softAP(ssid, password);

    Serial.begin(9600);
    

    ArduinoOTA.setHostname("esp32-ota");
    ArduinoOTA.begin();

    pinMode(MD[0], OUTPUT); 
    pinMode(MD[1], OUTPUT); 
    
    pinMode(bootButtonPin, INPUT_PULLUP);
    
    Wire.begin(I2C_SDA_PIN, I2C_SCL_PIN);
    tof_init();
}

void loop() {
    ArduinoOTA.handle();

    bool buttonState = digitalRead(bootButtonPin);
    if (buttonState != lastButtonState) {
        lastDebounceTime = millis();
        lastButtonState = buttonState;
    }

    if ((millis() - lastDebounceTime) > debounceDelay) {
        if (buttonState == LOW) {
            bool previousState = motorsEnabled;
            motorsEnabled = !motorsEnabled;

            while (digitalRead(bootButtonPin) == LOW);

            if (motorsEnabled && !previousState) {
                delay(5000);
            }
        }
    }

    if (!motorsEnabled) {
        analogWrite(MD[0], 0);
        analogWrite(MD[1], 0);
        return;
    }

    unsigned long now = micros();
    dt = (now - lastTime) / 1000000.0;
    lastTime = now;

    int total = 0;
    int weightedSum = 0;

    for (int i = 0; i < 5; i++) {
        int value = read_tof_distance(SensorIndex[i]); 
        weightedSum += value * weights[i];
        total += value;
    }

    float position = (total > 0) ? (float)weightedSum / total : 0;

    error = 0 - position;
    integral += error * dt; 
    float derivative = (error - previous_error) / dt;
    float correction = Kp * error + Ki * integral + Kd * derivative;
    previous_error = error;

    int leftMotor = constrain(baseSpeed + correction, 20, 255);
    int rightMotor = constrain(baseSpeed - correction, 20, 255);

    analogWrite(MD[1], leftMotor);
    analogWrite(MD[0], rightMotor);
}

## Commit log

2025-12-04 Create cad
2025-12-04 Create pcb
2025-12-04 new folders and Made the VL53L0X 3d model
    [VL53L0X.FCStd]
2025-12-04 Added a Photo of the 3d ToF sensor
2025-12-04 Added the .stl of ToF in 3d
    [VL53L0X-V2.stl]
2025-12-04 README update
    Added a Bill of Materials section on README
2025-12-04 New components
    Updated the Bill of Materials section with new items and prices.
2025-12-05 Made the Motors and motor driver
    [CYTRON-MDD3A.stl, DcMotor.FCStd, DcMotor.stl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]
2025-12-05 Made 3d models for esp32 and MDD3A
    [ESP32.FCStd, ESP32.stl, MDD3A.FCStd]
2025-12-05 Made the first version of the motor mount
    [MotorMountV1.stl]
2025-12-05 New Motor Mount , Updated README.md, added STLs folder for the future
    [MotorMountV2.FCStd, MotorMountV2.stl, Wheel.FCStd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]
2025-12-05 fixed some falses
    [MotorMount.FCStd, MotorMount.stl, MotorMountV1.stl]
2025-12-06 Base V1
    [Base.FCStd, Base.stl]
2025-12-06 Front Bumper .stl and .FCStd
    [FrontBumper.FCStd, FrontBumper.stl]
2025-12-08 Made holes to base for front and side bumpers
    [Base.FCStd]
2025-12-08 Made Side Bumper for right and left
    [SideBumper.FCStd, SideBumper.stl]
2025-12-08 Updated base for MDD3A Motor Driver
    [Base.FCStd, Base.stl]
2025-12-08 Updated the name of the file
    [CYTRON-MDD3A.FCStd]
2025-12-08 Updated JOURNAL.md
    [MDD3A.FCStd]
2025-12-09 Updated Base for the folkrace robot
    [Base.FCStd, Base.stl]
2025-12-09 MotorMount Photo
2025-12-09 Made Back bumper for the back of the robot
    [BackBumper.FCStd]
2025-12-09 added .stl of BackBumper
    [BackBumper.stl]
2025-12-09 base, and mounts update
    [Base.FCStd, Base.stl, MotorMount.FCStd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]
2025-12-09 Updated Rear Bumper
    [RearBumper.FCStd, RearBumper.stl]
2025-12-09 Final 3D Model
    [Final.FCStd]
2025-12-09 Added Final Photos
    [BackBumper.FCStd, BackBumper.stl]
2025-12-13 Made the pcb scematic
2025-12-13 updated PCB
    [FolckracePCB.kicad_pcb, FolckracePCB.kicad_sch, pcb.kicad_pcb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]
2025-12-14 New Base.svg
    [FolckracePCB.kicad_pcb, FolckracePCB.kicad_sch]
2025-12-15 Updated Base
    [Base.FCStd]
2025-12-15 Made svg files
    [BaseTraces.FCStd]
2025-12-16 updated parts
    [Base.stl, FrontBumper.FCStd, FrontBumper.stl]
2025-12-17 Ready for print
    [FrontBumper.stl, MotorMount.stl, RearBumper.stl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]
2025-12-17 Added all compoments
    [bom.csv]
2025-12-29 New top cover
    [TopCover.FCStd]
